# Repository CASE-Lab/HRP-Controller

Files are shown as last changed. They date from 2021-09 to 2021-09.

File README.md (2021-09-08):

# Unicorn HRP Controller

ROS and ROS2 packages for controller unicorn demo with HRP and SP. Also includes microcontroller code for controlling lights, actuators and distance sensors.

## Repository content

* catkin_ws
  * Contains a subset of the code from the [Husqvarna Research Platform](https://github.com/HusqvarnaResearch/hrp) repository.
    Gazebo simulation parts have been removed and only the necessary packages for control of the HRP hardware remain.
  
* colcon_ws
  * hw_controller:
    
    ROS2 node that communicates via serial to the microcontroller that is responsible for interfacing with the garbage tipper, garbage sensors (detects if there is garbage placed on the platform), distance sensors for collision avoidance and LED light strips for status indication.
    
  * unicorn_hrp:
    
    ROS2 node that controls the HRP hardware
    
  * hrp_msgs:
    
    Custom ROS messages
  
* hw-interface

  * Holds code for the microcontroller that interfaces directly with the additional sensors and actuators added to the HRP. Is controlled by the ROS 2 node hw_controller.

## Installation

The current system has been tested on either a Nvidia Jetson Nano or Jetson Xavier NX. The following dependencies need to be installed for the system to work properly:

* ROS2 eloquent [guide](https://index.ros.org/doc/ros2/Installation/Eloquent/Linux-Install-Debians/)

* ROS melodic [guide](http://wiki.ros.org/melodic/Installation/Ubuntu)

* ROS Bridge
  
Used to run a dynamic bridge that translates topics between the ROS2 and ROS. Can be installed by running:
  
  ```bash
  sudo apt-get update
  sudo apt install ros-eloquent-ros1-bridge
```
  
* [Pyserial](https://pypi.org/project/pyserial/) 
  
Needed for serial communication with the microcontroller hardware.
  
* GNU Screen 
  
  Used for the hrp_start.sh script that starts up the system
  Check out this [Quick Reference](https://gist.github.com/jctosta/af918e1618682638aa82) on how to use Screen.

By default Ubuntu does not allow users access to system serial ports. To solve this we need to add the current user to the dialout group:

```bash
sudo usermod -a -G dialout $USER
```

## Startup

Preparing the HRP for startup

1. Make sure the power switch is in the on position
2. Open the lid and enter code 1111
3. Wait for the HRP to initialize and then press start and close the lid when prompted to

Run the startup shell script from the repository root folder

```bash
./hrp_startup.sh
```

This will launch and automatically connect to a screen sessions with the following windows:

0. ros-bash
   
   Regular terminal window with bash and ROS sourced
   
1. am_driver

   Driver used to communicate with the HRP hardware

2. ros1_bridge

   Bridge used to bidirectionally translate topics from ROS2 and ROS

3. teleop

   Teleoperation and status of the HRP hardware

4. ros2_hw_controller

   ROS2 node for interfacing with microcontroller 

5. ros2_hrp_controller

   ROS2 node for interfacing with am_driver

Troubleshooting:

* am_driver is configured to launch with LOOP_OFF (the HRP in regular operation detects a wire signal to prevent it from going outside a specific area) but this does not always take effect. If this is the case navigate to the teleop window in screen and set LOOP_OFF manually

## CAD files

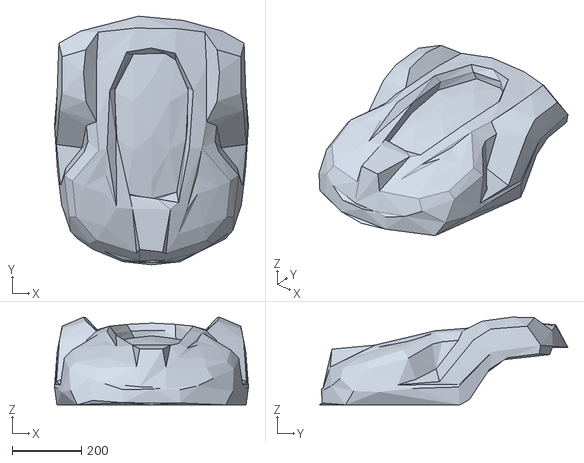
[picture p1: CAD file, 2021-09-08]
catkin_ws/src/am_description/urdf/am_chassis.stl
559.2 x 716.8 x 252.9

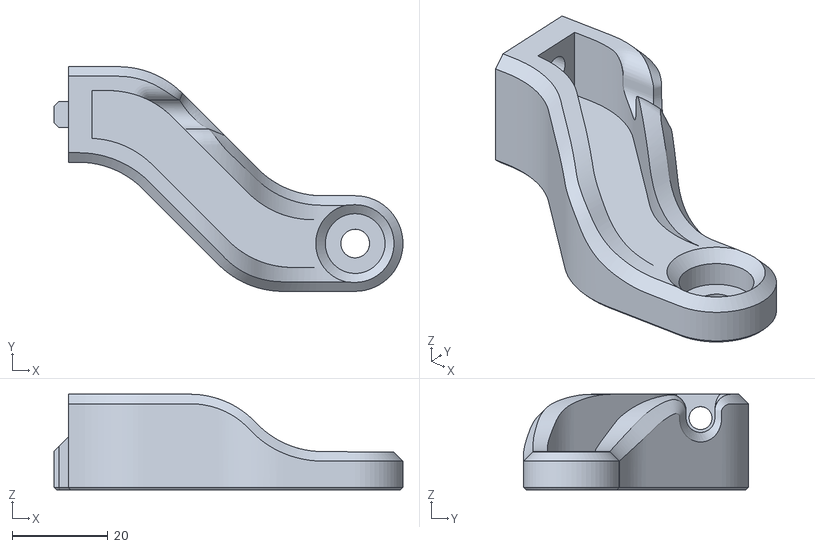
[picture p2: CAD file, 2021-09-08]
hardware/CAD_Garbage_Holder/ManufaturingFiles/RodHolder_Front3.stl
73.0 x 47.0 x 20.0

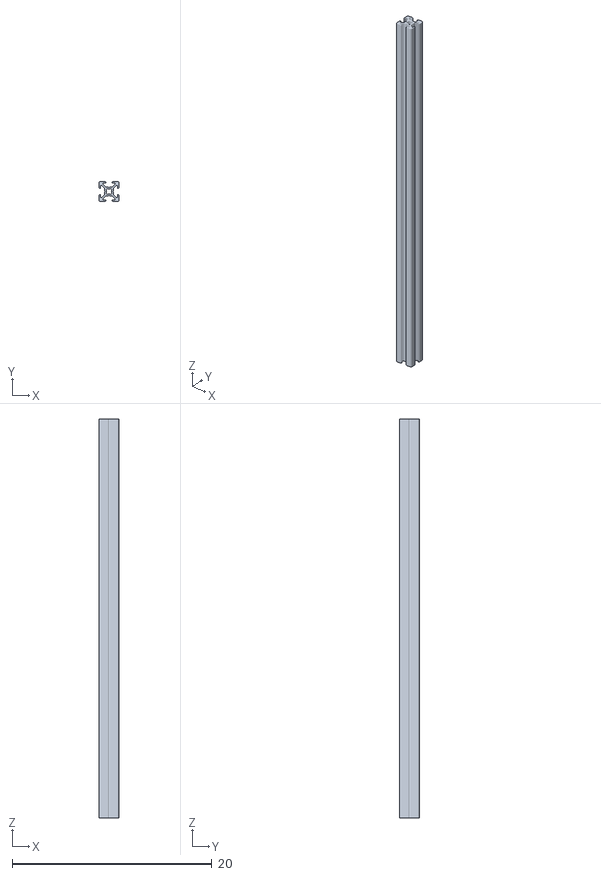
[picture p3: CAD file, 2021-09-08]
hardware/CAD_Garbage_Holder/Parts/Rexroth-3 842 992 888_230MM.stl
2.00 x 2.00 x 40.0

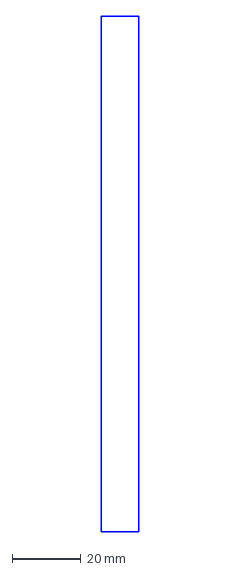
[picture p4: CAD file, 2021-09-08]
hardware/rgb-led-pcb/Outline.dxf
10.8 x 149.6 mm

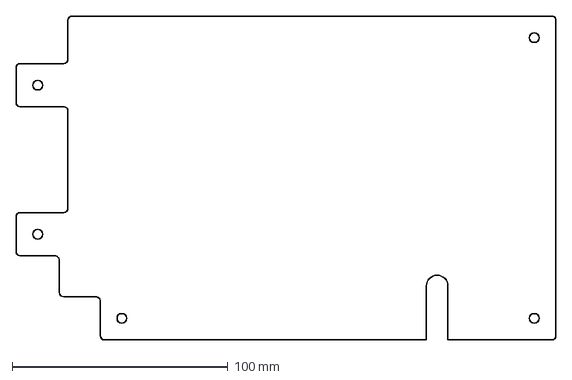
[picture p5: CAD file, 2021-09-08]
hardware/CAD_Garbage_Holder/ManufaturingFiles/SideAcrylicSheet.dxf
250.0 x 150.0 mm

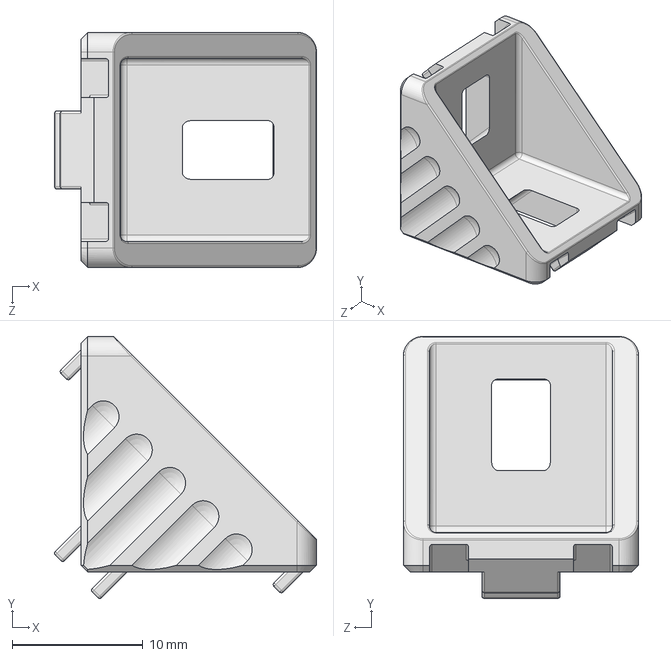
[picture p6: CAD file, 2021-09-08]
hardware/CAD_Garbage_Holder/Parts/Rexroth-3 842 523 508.step
20.0 x 20.0 x 18.0 mm

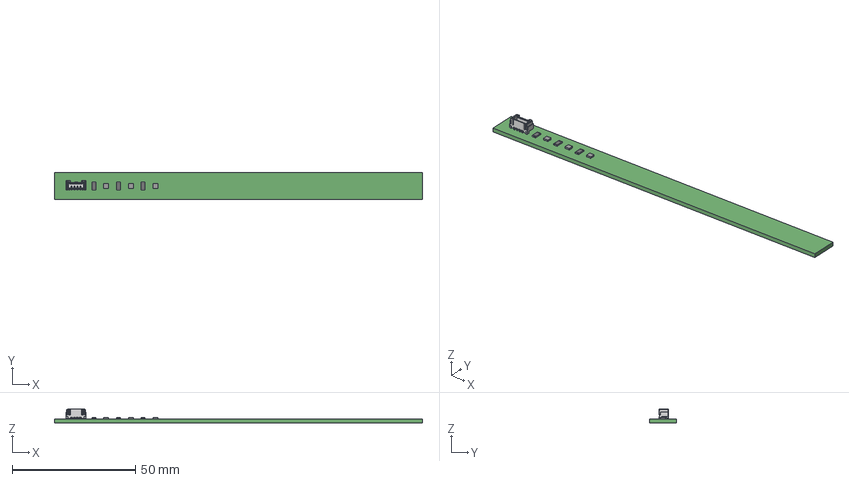
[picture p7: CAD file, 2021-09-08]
hardware/rgb-led-pcb/rgb-led-pcb.step
149.6 x 10.8 x 5.81 mm

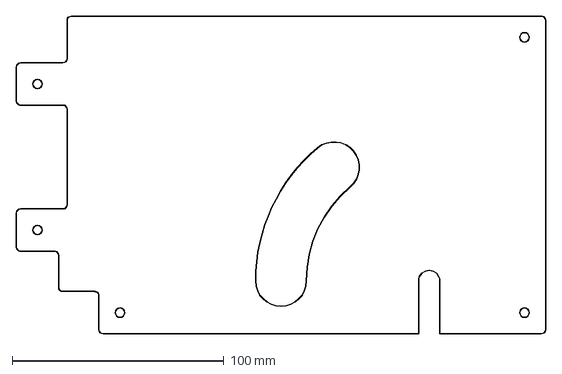
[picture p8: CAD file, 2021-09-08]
hardware/CAD_Garbage_Holder/ManufaturingFiles/SideAcrylicSheet_WithOpening.dxf
250.0 x 150.0 mm

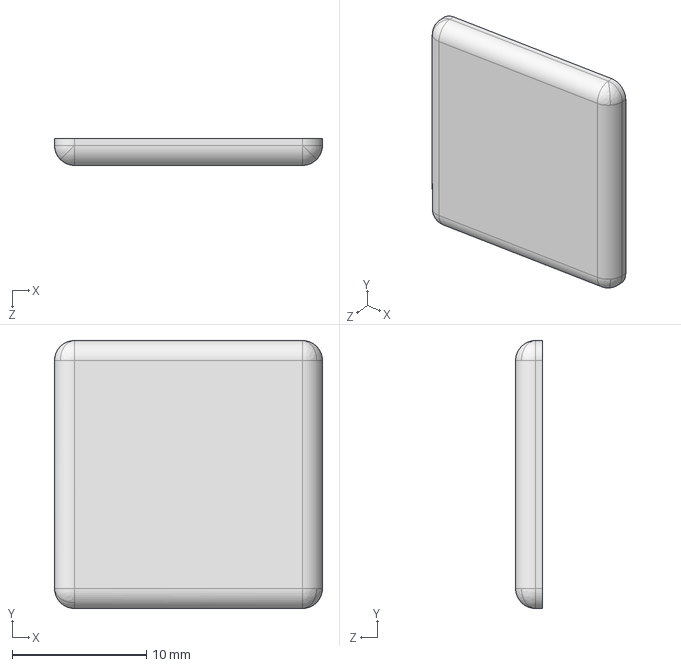
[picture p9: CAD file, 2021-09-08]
hardware/CAD_Garbage_Holder/Parts/Rexroth-3 842 517 243.step
20.0 x 20.0 x 2.00 mm

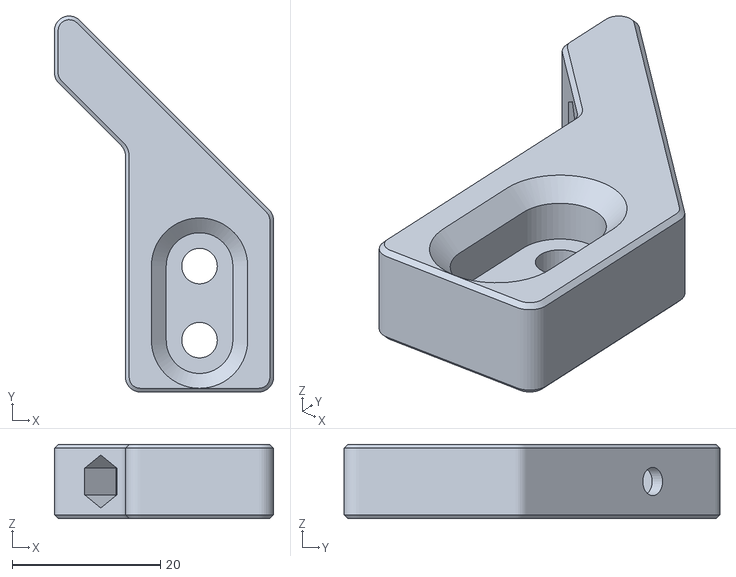
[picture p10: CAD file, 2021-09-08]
hardware/CAD_Garbage_Holder/ManufaturingFiles/UpperAcrylicSheetHolder_MIR.stl
29.6 x 50.8 x 10.0

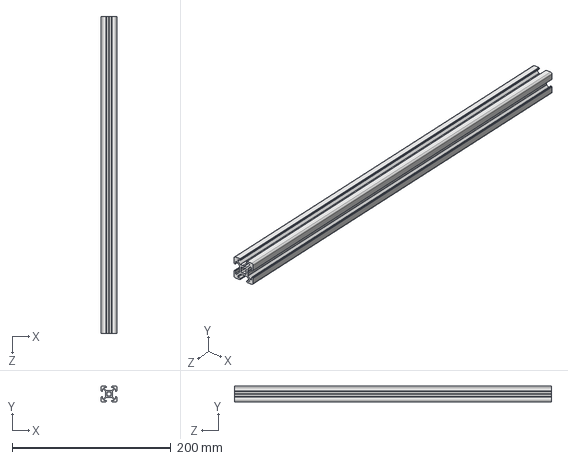
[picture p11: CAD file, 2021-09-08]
hardware/CAD_Garbage_Holder/Parts/Rexroth-3 842 992 888_400MM.step
20.0 x 20.0 x 400.0 mm

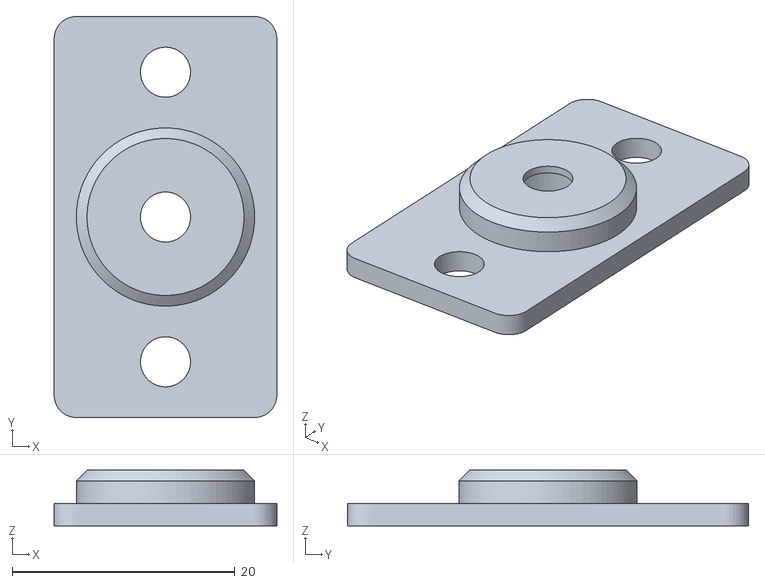
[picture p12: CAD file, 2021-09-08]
hardware/CAD_Garbage_Holder/ManufaturingFiles/LinearActuatorHolder_FlatHead.stl
20.0 x 36.0 x 5.00

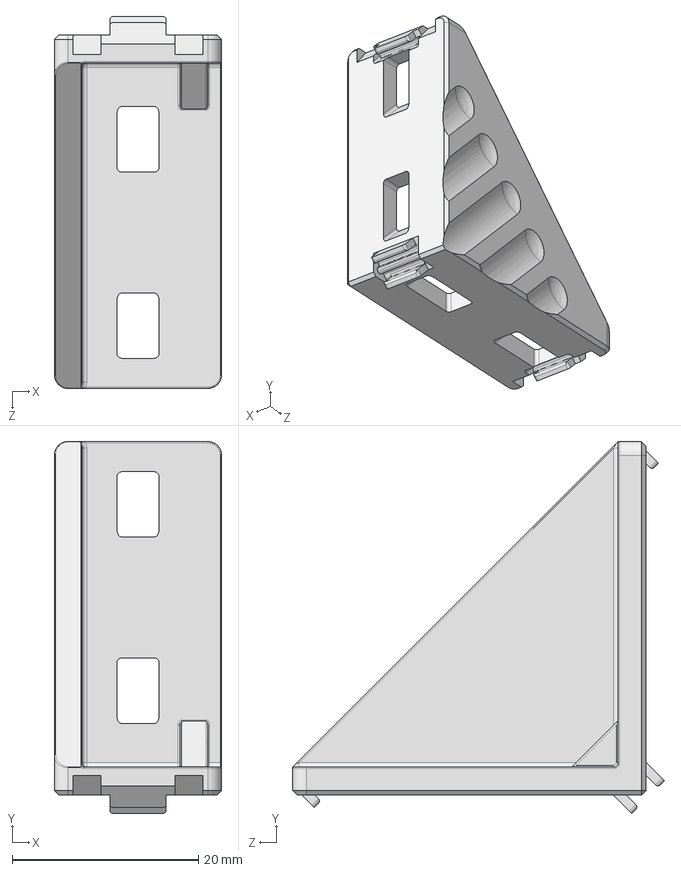
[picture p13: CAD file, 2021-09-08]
hardware/CAD_Garbage_Holder/Parts/Rexroth-3 842 523 517.step
18.0 x 40.0 x 40.0 mm

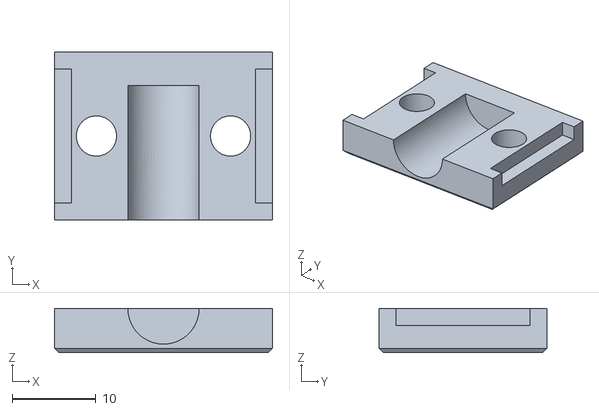
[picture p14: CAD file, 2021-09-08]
hardware/CAD_Garbage_Holder/ManufaturingFiles/SideAcrylicSheetRodHolder_1.stl
26.0 x 20.0 x 5.25

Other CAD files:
hardware/CAD_Garbage_Holder/Parts/LD3 Standard.STEP
hardware/CAD_Garbage_Holder/ManufaturingFiles/BackAcrylicSheet.dxf
hardware/CAD_Garbage_Holder/ManufaturingFiles/BottomAcrylicSheetHolder.stl
hardware/CAD_Garbage_Holder/ManufaturingFiles/SideAcrylicSheetRodHolder_2.stl
hardware/CAD_Garbage_Holder/ManufaturingFiles/BottomAcrylicSheet.dxf
hardware/CAD_Garbage_Holder/ManufaturingFiles/BottomAcrylicSheetRodHolder_1.stl
hardware/CAD_Garbage_Holder/ManufaturingFiles/BottomAcrylicSheetRodHolder_2.stl
hardware/CAD_Garbage_Holder/ManufaturingFiles/Bumper.stl
hardware/CAD_Garbage_Holder/ManufaturingFiles/CableHolder.stl
hardware/CAD_Garbage_Holder/ManufaturingFiles/Controller_PCB_outline.dxf
hardware/CAD_Garbage_Holder/ManufaturingFiles/DistanceSensorHolder.stl
hardware/CAD_Garbage_Holder/ManufaturingFiles/HRP_button_glass.dxf
hardware/CAD_Garbage_Holder/ManufaturingFiles/HolderBack.stl
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

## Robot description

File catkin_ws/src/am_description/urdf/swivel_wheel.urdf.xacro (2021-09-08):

<?xml version="1.0"?>
<robot name="swivel_wheel" xmlns:xacro="http://www.ros.org/wiki/xacro">

  <!-- Wheels -->
<!--
  <xacro:property name="wheel_radius" value="0.125" />
  <xacro:property name="wheel_height" value="0.032" />
-->
  <xacro:property name="wheel_mass" value="0.5" /> <!-- in kg-->

<!--
  <xacro:property name="base_x_origin_to_wheel_origin" value="0.25" />
  <xacro:property name="base_y_origin_to_wheel_origin" value="0.3" />
  <xacro:property name="base_z_origin_to_wheel_origin" value="0.0" />
-->

  <xacro:macro name="cylinder_inertia" params="m r h">
    <inertia ixx="${m*(3*r*r+h*h)/12}" ixy="0" ixz="0" iyy="${m*(3*r*r+h*h)/12}" iyz="0" izz="${m*r*r/2}" />
  </xacro:macro>

  <xacro:macro name="swivel_arm" params="lr index l offset">
    <link name="sw_arm_${lr}_${index}">

      <inertial>
        <mass value="0.01" />
        <origin xyz="0 0 0" />
        <cylinder_inertia m="0.01" r="0.004" h="${l}" />
      </inertial>

      <visual>
        <geometry>
          <cylinder radius="0.004" length="${l}" />
        </geometry>
        <material name="silver">
          <color rgba="0.3 0.3 0.3 1" />
        </material>
        <origin rpy="0 0 0" xyz="${offset}" />
      </visual>
    </link>
  </xacro:macro>

  <xacro:macro name="swivel_wheel" params="fb lr parent translateX translateY translateZ wheel_radius wheel_height flip"> <!--fb : front, back ; lr: left, right -->

    <!-- First link connected to parent-->
    <swivel_arm lr="${lr}" index="1" l="0.06" offset="0 0 -0.03" />

    <joint name="sw_arm_${lr}_connect_1" type="continuous">
      <origin xyz="${translateX} ${translateY} ${translateZ}" rpy="0 0 0" />
      <axis xyz="0 0 1" rpy="0 0 0" />
      <parent link="${parent}" />
      <child link="sw_arm_${lr}_1" />
      <limit effort="100" velocity="100" />
      <joint_properties damping="0.0" friction="0.0" />
    </joint>

    <!-- Second link connected to first-->
    <swivel_arm lr="${lr}" index="2" l="0.04" offset="0 0 0.02" />

    <joint name="sw_arm_${lr}_connect_2" type="fixed">
      <origin rpy="1.5707 0 0" xyz="0 0 -0.06" />
      <parent link="sw_arm_${lr}_1" />
      <child link="sw_arm_${lr}_2" />
    </joint>

    <!-- Third link connected to second-->
    <swivel_arm lr="${lr}" index="3" l="0.06" offset="0 0 -0.03" />

    <joint name="sw_arm_${lr}_connect_3" type="fixed">
      <origin rpy="-1.5707 0 -0.78" xyz="0 0 0.04" />
      <parent link="sw_arm_${lr}_2" />
      <child link="sw_arm_${lr}_3" />
    </joint>

    <!-- Fourth link connected to third-->
    <swivel_arm lr="${lr}" index="4" l="0.04" offset="0 0 -0.02" />

    <joint name="sw_arm_${lr}_connect_4" type="fixed">
      <origin rpy="1.5707 0 0" xyz="0 0 -0.060" />
      <parent link="sw_arm_${lr}_3" />
      <child link="sw_arm_${lr}_4" />
    </joint>

    <!-- Wheel connected to fourth-->
    <link name="${fb}_${lr}_swivel_wheel">
      <visual>
        <origin xyz="0 0 0" rpy="${flip*M_PI/2} 0 0" />
        <geometry>
          <cylinder length="${wheel_height}" radius="${wheel_radius}" />
        </geometry>
        <material name="Black" />
      </visual>
      <collision>
        <origin xyz="0 0 0" rpy="0 0 0" />
        <geometry>
          <cylinder length="${wheel_height}" radius="${wheel_radius}" />
        </geometry>
      </collision>
      <inertial>
        <mass value="${wheel_mass}" />
        <origin xyz="0 0 0" />
        <cylinder_inertia m="${wheel_mass}" r="${wheel_radius}" h="${wheel_height}" />
      </inertial>
    </link>

    <gazebo reference="${fb}_${lr}_swivel_wheel">
      <mu1 value="0.8" />
      <mu2 value="0.8" />
      <kp value="10000000.0" />
      <kd value="1.0" />
      <fdir1 value="1 0 0" />
      <material>Gazebo/Black</material>
      <turnGravityOff>false</turnGravityOff>
    </gazebo>

    <joint name="${fb}_${lr}_swivel_wheel_joint" type="continuous">
      <parent link="sw_arm_${lr}_4" />
      <child link="${fb}_${lr}_swivel_wheel" />
      <origin rpy="0 0 0" xyz="0 0 -0.04" />
      <axis xyz="0 0 1" rpy="0 0 0" />
      <limit effort="100" velocity="100" />
      <joint_properties damping="0.0" friction="0.0" />
    </joint>


    <!-- Transmission is important to link the joints and the controller -->
<!--
    <transmission name="${fb}_${lr}_swivel_wheel_joint_trans">
      <type>transmission_interface/SimpleTransmission</type>
      <joint name="${fb}_${lr}_swivel_wheel_joint">
        <hardwareInterface>EffortJointInterface</hardwareInterface>
      </joint>
      <actuator name="${fb}_${lr}_swivel_wheel_joint_motor">
        <hardwareInterface>EffortJointInterface</hardwareInterface>
        <mechanicalReduction>1</mechanicalReduction>
      </actuator>
    </transmission>
-->


  </xacro:macro>
</robot>

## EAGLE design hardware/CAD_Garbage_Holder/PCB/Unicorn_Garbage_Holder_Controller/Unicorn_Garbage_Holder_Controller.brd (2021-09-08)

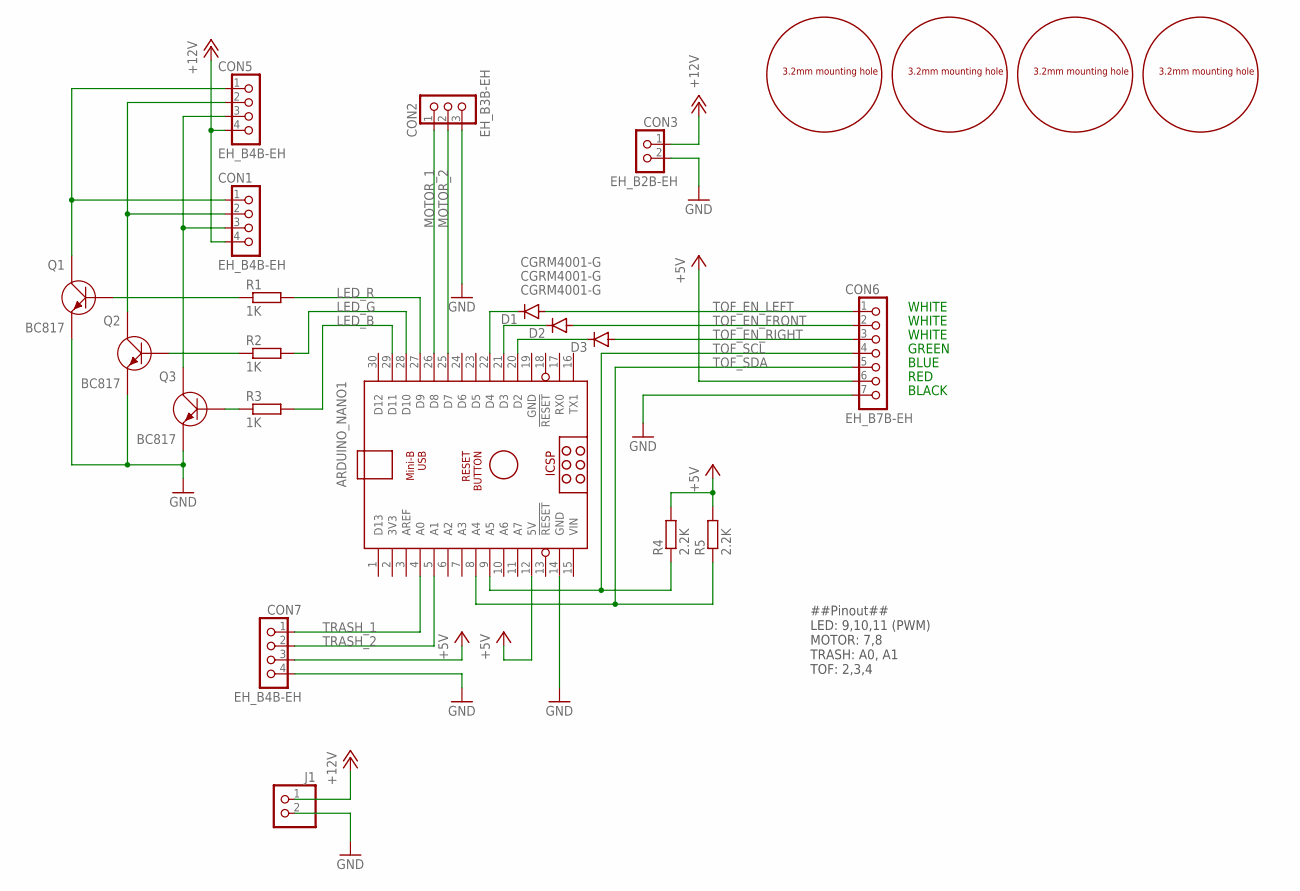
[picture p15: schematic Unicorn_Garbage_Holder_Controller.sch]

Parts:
ARDUINO_NANO1: ARDUINO_NANO
CON1, CON5, CON7: EH_B4B-EH; B4B-EH
CON2: EH_B3B-EH; B3B-EH
CON3: EH_B2B-EH; B2B-EH
CON6: EH_B7B-EH; B7B-EH
D1, D2, D3: CGRM4001-G; SOD-123_MINI-SMA
J1: 1751248
Q1, Q2, Q3: BC817; SOT23
R1, R2, R3: 1K; R0603
R4, R5: 2.2K; R0603
U$5, U$6, U$7, U$8: M3_MOUNTING_HOLE

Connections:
+5V: ARDUINO_NANO1.12 (5V), CON6.6, CON7.3, R4.2, R5.2
+12V: CON1.4, CON3.1, CON5.4, J1.1
GND: ARDUINO_NANO1.14 (GND), ARDUINO_NANO1.19 (GND), CON2.3, CON3.2, CON6.7, CON7.4, J1.2, Q1.2 (E), Q2.2 (E), Q3.2 (E)
LED_B: ARDUINO_NANO1.29 (D11), R3.2
LED_G: ARDUINO_NANO1.28 (D10), R2.2
LED_R: ARDUINO_NANO1.27 (D9), R1.2
MOTOR_1: ARDUINO_NANO1.26 (D8), CON2.1
MOTOR_2: ARDUINO_NANO1.25 (D7), CON2.2
unnamed: Q1.1 (B), R1.1
unnamed: Q2.1 (B), R2.1
unnamed: Q3.1 (B), R3.1
unnamed: CON1.1, CON5.1, Q1.3 (C)
unnamed: CON1.2, CON5.2, Q2.3 (C)
unnamed: CON1.3, CON5.3, Q3.3 (C)
unnamed: ARDUINO_NANO1.22 (D4), D1.C
unnamed: ARDUINO_NANO1.21 (D3), D2.C
unnamed: ARDUINO_NANO1.20 (D2), D3.C
TOF_EN_FRONT: CON6.2, D2.A
TOF_EN_LEFT: CON6.1, D1.A
TOF_EN_RIGHT: CON6.3, D3.A
TOF_SCL: ARDUINO_NANO1.9 (A5), CON6.4, R4.1
TOF_SDA: ARDUINO_NANO1.8 (A4), CON6.5, R5.1
TRASH_1: ARDUINO_NANO1.4 (A0), CON7.1
TRASH_2: ARDUINO_NANO1.5 (A1), CON7.2
VIN: ARDUINO_NANO1.15 (VIN)

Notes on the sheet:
##Pinout## LED: 9,10,11 (PWM) MOTOR: 7,8 TRASH: A0, A1 TOF: 2,3,4
BLUE
GREEN
WHITE
RED
BLACK

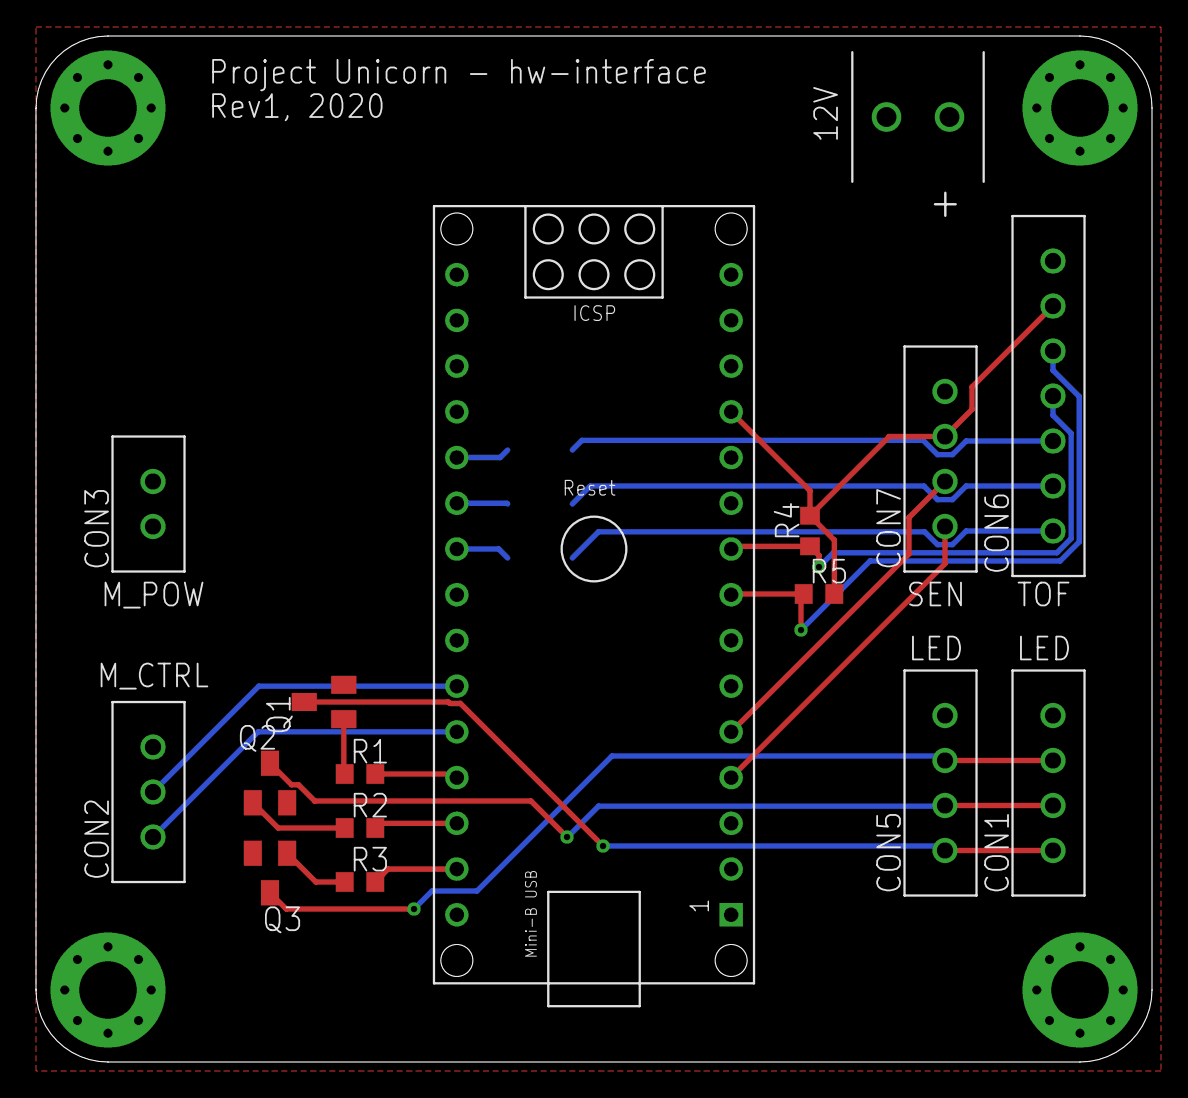
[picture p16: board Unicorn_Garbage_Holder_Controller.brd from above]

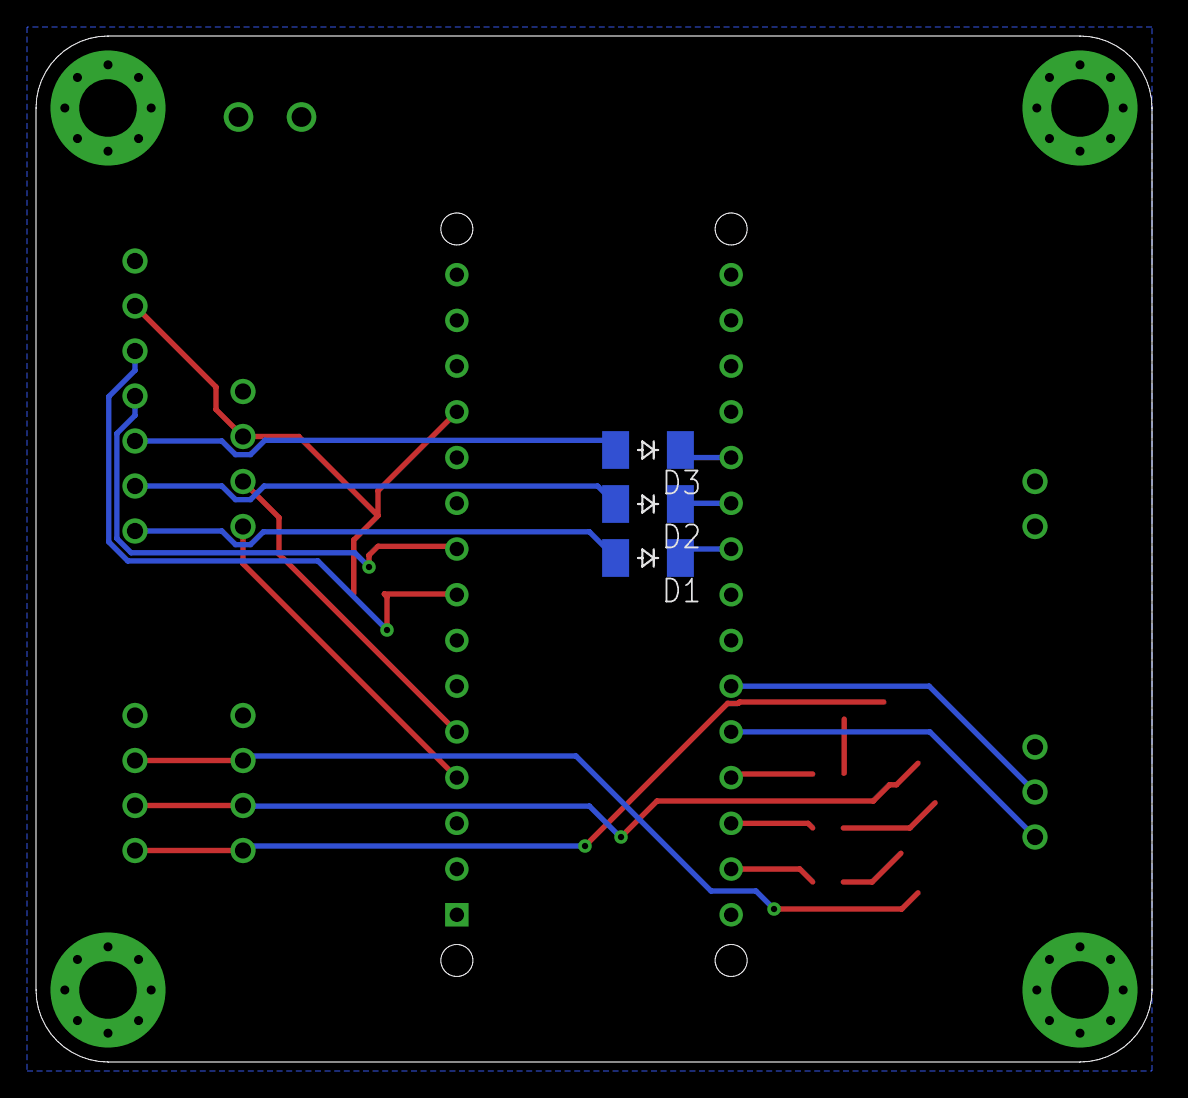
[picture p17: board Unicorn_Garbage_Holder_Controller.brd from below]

Board: 2 copper layers, 62.0 x 57.0 mm, 23 parts (3 on the bottom side), 24 nets.

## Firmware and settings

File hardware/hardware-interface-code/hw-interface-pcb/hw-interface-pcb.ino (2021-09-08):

#include "src/Adafruit-VL530X/Adafruit_VL53L0X.h"
#include "TrashActuator.h"

//all serial commands are sent in a single byte where only the latest
//command is considered

#define NEWLINE "\n"

//defenition of serial commands:
#define ACTUATOR_MASK   0b00000011
#define ACTUATOR_SHIFT  0
#define COLOR_MASK      0b00011100
#define COLOR_SHIFT     2

// address we will assign if dual sensor is present
#define LOXR_ADDRESS 0x30
#define LOXF_ADDRESS 0x31
// last one will be left with default adress 0x29

// set the pins to shutdown
#define SHT_LOXR 2 //right (diode connected
#define SHT_LOXF 3 //front (diode connected)
#define SHT_LOXL 4 //left  (diode connected)

//define sensor states
#define LOX_OUT_OF_RANGE 4
#define LOX_ERROR -2

// objects for the vl53l0x
Adafruit_VL53L0X loxRight = Adafruit_VL53L0X();
Adafruit_VL53L0X loxFront = Adafruit_VL53L0X();
Adafruit_VL53L0X loxLeft = Adafruit_VL53L0X();

//define pins for indicator light
#define R_OUT (uint8_t)9
#define G_OUT (uint8_t)10
#define B_OUT (uint8_t)11

//define colors for indicator light
#define INDICATOR_OFF 0
#define INDICATOR_RED 1
#define INDICATOR_BLUE 2
#define INDICATOR_GREEN 3
#define INDICATOR_YELLOW 4
#define INDICATOR_WHITE 5

//global variable for current color
uint8_t currentColor;

//function prototypes for indicator light
void setColor(uint8_t color);
void initIndicator();

// set the pins for motor control
#define IN1 8
#define IN2 7

// sets actuation time in ms
#define ACTUATION_TIME 4000

// object for trash tipper
TrashActuator actuator = TrashActuator(IN1, IN2, ACTUATION_TIME);

//function prototypes:
void setID();
int readRange(Adafruit_VL53L0X *sensor);

//pin defenitions for trash sensors
#define PROX_PIN1 A0
#define PROX_PIN2 A1

//trash status values
#define TRASH_FULL 1
#define TRASH_EMPTY 0
#define TRASH_FULL_PATTERN   0b00000011 //sets how many consequtive readings need to be the same for state switch
#define TRASH_EMPTY_PATTERN  0b00000000
#define TRASH_PATTERN_MASK   0b00000011 //sets how many consequtive readings need to be the same for state switch

void setup() {
  Serial.begin(115200);
  // wait until serial port opens for native USB devices:
  while (! Serial) { delay(1); }

  //configure adress for all 3 sensors:
  setID();

  //set actuator to down position
  actuator.setActuatorCommand(ACTUATOR_CMD_DOWN
  , millis());
  //delay(ACTUATION_TIME);

  //configure trash sensors pins as input:
  pinMode(PROX_PIN1, INPUT);
  pinMode(PROX_PIN2, INPUT);

  initIndicator();
  
  //testing colors:
  setColor(INDICATOR_RED);
  delay(100);
  setColor(INDICATOR_GREEN);
  delay(100);
  setColor(INDICATOR_BLUE);
  delay(100);
  setColor(INDICATOR_YELLOW);
  delay(100);
  setColor(INDICATOR_WHITE);
  delay(100);
  setColor(INDICATOR_GREEN);   //default standby color
}

void loop() {

  //set up static local variables;
  static int rightRange, leftRange, frontRange;
  static unsigned long timeInterval;
  static char tempCmd;
  static uint8_t cmd = 0;
  static uint8_t trashStatus;
  static uint8_t trashStatusDebounce = 0;
  static uint8_t cmdColor;
  static uint8_t cmdActuator;
  uint8_t prevCmd = cmd;

  // grab latest command (reads serial buffer until empty)
  while( (tempCmd = Serial.read()) != -1 ) {
    cmd = tempCmd;
  }

  //check if command has changed:
  if(cmd!=prevCmd) {
    // Serial.print(F("NEW CMD: "));
    // Serial.println(cmd, BIN);
    //parse commands:
    cmdActuator = (cmd & ACTUATOR_MASK) >> ACTUATOR_SHIFT;
    cmdColor = (cmd & COLOR_MASK) >> COLOR_SHIFT;
    // Serial.print(F("NEW CMD ACTUATOR: "));
    // Serial.println(cmdActuator, BIN);
    // Serial.print(F("NEW CMD COLOR: "));
    // Serial.println(cmdColor, BIN);

    //set commands:
    actuator.setActuatorCommand(cmdActuator, millis());
    setColor(cmdColor);
  }

  //read distances:
  rightRange = readRange(&loxRight);
  leftRange = readRange(&loxLeft);
  frontRange = readRange(&loxFront);

  //check sensor error status:
  while(rightRange == LOX_ERROR || leftRange == LOX_ERROR || frontRange == LOX_ERROR) {
    //reset sensors:
    setID();
    //read distances:
    rightRange = readRange(&loxRight);
    leftRange = readRange(&loxLeft);
    frontRange = readRange(&loxFront);
  }

  //read status of trash proximity sensors
  //if any of the sensor are active low then trash is considered detected

  if (!digitalRead(PROX_PIN1) || !digitalRead(PROX_PIN2)) {
    trashStatusDebounce = trashStatusDebounce << 1;
    trashStatusDebounce |= 1;
  }
  else {
    trashStatusDebounce = trashStatusDebounce << 1;
  }

  if ( (trashStatusDebounce & TRASH_PATTERN_MASK) == TRASH_FULL_PATTERN) {
    trashStatus = TRASH_FULL;
  }
  else if ( (trashStatusDebounce & TRASH_PATTERN_MASK) == TRASH_EMPTY_PATTERN) {
    trashStatus = TRASH_EMPTY;
  }

  //trash debounce debug:
/*   Serial.print("Trash Status: ");
  Serial.println(trashStatus);
  Serial.print("History: ");
  Serial.println(trashStatusDebounce, BIN); */
  
  //indicate start of packet
  Serial.print(F("PACKET:"));
  Serial.print(NEWLINE);
  //print range over serial:
  Serial.print(F("R: "));
  Serial.print(rightRange);
  Serial.print(NEWLINE);
  Serial.print(F("L: "));
  Serial.print(leftRange);
  Serial.print(NEWLINE);
  Serial.print(F("F: "));
  Serial.print(frontRange);
  Serial.print(NEWLINE);

  //print state of trash actuator
  Serial.print(F("A: "));
  Serial.print(actuator.getActuatorState(millis()));
  Serial.print(NEWLINE);

  //print state of trash carrying
  Serial.print(F("T: "));
  Serial.print(trashStatus);
  Serial.print(NEWLINE);

  //print state of ligt indicator
  Serial.print(F("I: "));
  Serial.print(currentColor);
  Serial.print(NEWLINE);
}


void setID() {
  Serial.println(F("Resetting sensors"));
  // shutdown all sensors:
  pinMode(SHT_LOXR, OUTPUT);
  pinMode(SHT_LOXF, OUTPUT);
  pinMode(SHT_LOXL, OUTPUT);

  digitalWrite(SHT_LOXR, LOW);
  digitalWrite(SHT_LOXF, LOW);
  digitalWrite(SHT_LOXL, LOW);

  delay(10);

  // enable right sensor:
  pinMode(SHT_LOXR, INPUT);
  delay(10);

  // initing right
  if(!loxRight.begin(LOXR_ADDRESS)) {
    Serial.println(F("Right failed"));
    while(1);
  }
  delay(10);

  //enable front sensor:
  pinMode(SHT_LOXF, INPUT);
  delay(10);

  //initing front
  if(!loxFront.begin(LOXF_ADDRESS)) {
    Serial.println(F("Front failed"));
    while(1);
  }
  delay(10);

  //enable left sensor
  pinMode(SHT_LOXL, INPUT);
  delay(10);
  
  //initing left (default adress)
  if(!loxLeft.begin()) {
    Serial.println(F("Left failed"));
    while(1);
  }
  delay(10);
}

int readRange(Adafruit_VL53L0X *sensor) {
  int status;
  // returns -1 if sensor is out of range
  // returns range  in mm if sensor is in range
  // this holds the measurement (what is this struct -  how much memmory?)
  static VL53L0X_RangingMeasurementData_t measurement;
  // get measurement with debug disabled
  status = sensor->getSingleRangingMeasurement(&measurement, false);
  //Serial.print(F("Status: "));
  //Serial.println(status);
  if(status == VL53L0X_ERROR_NONE) {
    if(measurement.RangeStatus != LOX_OUT_OF_RANGE) {
      return measurement.RangeMilliMeter;
    }
    else {
      return -1;
    }
  }
  else {
    //did not manage to read distance correctly
    return LOX_ERROR;
  }

}

void initIndicator() {
  pinMode(R_OUT, OUTPUT);
  pinMode(G_OUT, OUTPUT);
  pinMode(B_OUT, OUTPUT);

  digitalWrite(R_OUT, LOW);
  digitalWrite(G_OUT, LOW);
  digitalWrite(B_OUT, LOW);

  currentColor = INDICATOR_OFF;
}

void setColor(uint8_t color) {
    //Serial.println(F("Setting color"));
    currentColor = color;
    switch (color) {
    case INDICATOR_OFF:
      digitalWrite(R_OUT, LOW);
      digitalWrite(G_OUT, LOW);
      digitalWrite(B_OUT, LOW);
      break;

    case INDICATOR_RED:
      digitalWrite(R_OUT, HIGH);
      digitalWrite(G_OUT, LOW);
      digitalWrite(B_OUT, LOW);
      break;

    case INDICATOR_BLUE:
      digitalWrite(R_OUT, LOW);
      digitalWrite(G_OUT, LOW);
      digitalWrite(B_OUT, HIGH);
      break;

    case INDICATOR_GREEN:
      digitalWrite(R_OUT, LOW);
      digitalWrite(G_OUT, HIGH);
      digitalWrite(B_OUT, LOW);
      break;

    case INDICATOR_YELLOW:
      digitalWrite(R_OUT, HIGH);
      digitalWrite(G_OUT, HIGH);
      digitalWrite(B_OUT, LOW);
      break;

    case INDICATOR_WHITE:
      digitalWrite(R_OUT, HIGH);
      digitalWrite(G_OUT, HIGH);
      digitalWrite(B_OUT, HIGH);
      break;

    default:
        digitalWrite(R_OUT, LOW);
        digitalWrite(G_OUT, LOW);
        digitalWrite(B_OUT, LOW);
        break;
    }
}

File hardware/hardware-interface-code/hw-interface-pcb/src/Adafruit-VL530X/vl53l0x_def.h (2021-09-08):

/*******************************************************************************
Copyright 2016, STMicroelectronics International N.V.
All rights reserved.

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
THIS SOFTWARE IS PROVIDED BY THE COPYRIGHT HOLDERS AND CONTRIBUTORS "AS IS" AND
ANY EXPRESS OR IMPLIED WARRANTIES, INCLUDING, BUT NOT LIMITED TO, THE IMPLIED
WARRANTIES OF MERCHANTABILITY, FITNESS FOR A PARTICULAR PURPOSE, AND
NON-INFRINGEMENT OF INTELLECTUAL PROPERTY RIGHTS ARE DISCLAIMED.
IN NO EVENT SHALL STMICROELECTRONICS INTERNATIONAL N.V. BE LIABLE FOR ANY
DIRECT, INDIRECT, INCIDENTAL, SPECIAL, EXEMPLARY, OR CONSEQUENTIAL DAMAGES
(INCLUDING, BUT NOT LIMITED TO, PROCUREMENT OF SUBSTITUTE GOODS OR SERVICES;
LOSS OF USE, DATA, OR PROFITS; OR BUSINESS INTERRUPTION) HOWEVER CAUSED AND
ON ANY THEORY OF LIABILITY, WHETHER IN CONTRACT, STRICT LIABILITY, OR TORT
(INCLUDING NEGLIGENCE OR OTHERWISE) ARISING IN ANY WAY OUT OF THE USE OF THIS
SOFTWARE, EVEN IF ADVISED OF THE POSSIBILITY OF SUCH DAMAGE.
*******************************************************************************/

/**
 * @file VL53L0X_def.h
 *
 * @brief Type definitions for VL53L0X API.
 *
 */

#ifndef _VL53L0X_DEF_H_
#define _VL53L0X_DEF_H_

#ifdef __cplusplus
extern "C" {
#endif

/** @defgroup VL53L0X_globaldefine_group VL53L0X Defines
 *	@brief	  VL53L0X Defines
 *	@{
 */

/** PAL SPECIFICATION major version */
#define VL53L0X10_SPECIFICATION_VER_MAJOR 1
/** PAL SPECIFICATION minor version */
#define VL53L0X10_SPECIFICATION_VER_MINOR 2
/** PAL SPECIFICATION sub version */
#define VL53L0X10_SPECIFICATION_VER_SUB 7
/** PAL SPECIFICATION sub version */
#define VL53L0X10_SPECIFICATION_VER_REVISION 1440

/** VL53L0X PAL IMPLEMENTATION major version */
#define VL53L0X10_IMPLEMENTATION_VER_MAJOR 1
/** VL53L0X PAL IMPLEMENTATION minor version */
#define VL53L0X10_IMPLEMENTATION_VER_MINOR 0
/** VL53L0X PAL IMPLEMENTATION sub version */
#define VL53L0X10_IMPLEMENTATION_VER_SUB 9
/** VL53L0X PAL IMPLEMENTATION sub version */
#define VL53L0X10_IMPLEMENTATION_VER_REVISION 3673

/** PAL SPECIFICATION major version */
#define VL53L0X_SPECIFICATION_VER_MAJOR 1
/** PAL SPECIFICATION minor version */
#define VL53L0X_SPECIFICATION_VER_MINOR 2
/** PAL SPECIFICATION sub version */
#define VL53L0X_SPECIFICATION_VER_SUB 7
/** PAL SPECIFICATION sub version */
#define VL53L0X_SPECIFICATION_VER_REVISION 1440

/** VL53L0X PAL IMPLEMENTATION major version */
#define VL53L0X_IMPLEMENTATION_VER_MAJOR 1
/** VL53L0X PAL IMPLEMENTATION minor version */
#define VL53L0X_IMPLEMENTATION_VER_MINOR 0
/** VL53L0X PAL IMPLEMENTATION sub version */
#define VL53L0X_IMPLEMENTATION_VER_SUB 1
/** VL53L0X PAL IMPLEMENTATION sub version */
#define VL53L0X_IMPLEMENTATION_VER_REVISION 4606
#define VL53L0X_DEFAULT_MAX_LOOP 200
#define VL53L0X_MAX_STRING_LENGTH 8

#include "vl53l0x_device.h"
#include "vl53l0x_types.h"

/****************************************
 * PRIVATE define do not edit
 ****************************************/

/** @brief Defines the parameters of the Get Version Functions
 */
typedef struct {
  uint32_t revision; /*!< revision number */
  uint8_t major;     /*!< major number */
  uint8_t minor;     /*!< minor number */
  uint8_t build;     /*!< build number */
} VL53L0X_Version_t;

/** @brief Defines the parameters of the Get Device Info Functions
 */
typedef struct {
  char Name[VL53L0X_MAX_STRING_LENGTH];
  /*!< Name of the Device e.g. Left_Distance */
  char Type[VL53L0X_MAX_STRING_LENGTH];
  /*!< Type of the Device e.g VL53L0X */
  char ProductId[VL53L0X_MAX_STRING_LENGTH];
  /*!< Product Identifier String	*/
  uint8_t ProductType;
  /*!< Product Type, VL53L0X = 1, VL53L1 = 2 */
  uint8_t ProductRevisionMajor;
  /*!< Product revision major */
  uint8_t ProductRevisionMinor;
  /*!< Product revision minor */
} VL53L0X_DeviceInfo_t;

/** @defgroup VL53L0X_define_Error_group Error and Warning code returned by API
 *	The following DEFINE are used to identify the PAL ERROR
 *	@{
 */

typedef int8_t VL53L0X_Error;

#define VL53L0X_ERROR_NONE ((VL53L0X_Error)0)
#define VL53L0X_ERROR_CALIBRATION_WARNING ((VL53L0X_Error)-1)
/*!< Warning invalid calibration data may be in used
        \a	VL53L0X_InitData()
        \a VL53L0X_GetOffsetCalibrationData
        \a VL53L0X_SetOffsetCalibrationData */
#define VL53L0X_ERROR_MIN_CLIPPED ((VL53L0X_Error)-2)
/*!< Warning parameter passed was clipped to min before to be applied */
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

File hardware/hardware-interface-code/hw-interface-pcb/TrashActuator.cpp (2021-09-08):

#include "TrashActuator.h"
#include "Arduino.h"

TrashActuator::TrashActuator(uint8_t IN1, uint8_t IN2, unsigned long actuationTime) {
    this->IN1 = IN1;
    this->IN2 = IN2;
    this->actuationTime = actuationTime;

    //set up pin outputs
    pinMode(IN1, OUTPUT);
    pinMode(IN2, OUTPUT);

    //set up initial command and output to COAST
    digitalWrite(IN1, LOW);
    digitalWrite(IN2, LOW);

    currentCommand = ACTUATOR_CMD_COAST;

    //initial position when starting is unknown
    actuatorState = ACTUATOR_UNKOWN;

}

void TrashActuator::setActuatorCommand(uint8_t command, unsigned long currentTime) {
    //Serial.println(F("Setting command"));
    if(command == currentCommand) {
        return; //ignore repeated same command
    }
    else {
        currentCommand = command;
    }

    switch (command)
    {
    case ACTUATOR_CMD_UP:
        prevTime = currentTime; //sets timer
        actuatorState = ACTUATOR_UNKOWN;
        //set motor outputs:
        digitalWrite(IN1, HIGH);
        digitalWrite(IN2, LOW);
        break;

    case ACTUATOR_CMD_DOWN:
        //Serial.println(F("CMD: DOWM"));
        prevTime = currentTime; //sets timer
        actuatorState = ACTUATOR_UNKOWN;
        //set motor outputs:
        digitalWrite(IN1, LOW);
        digitalWrite(IN2, HIGH);
        break;

    case ACTUATOR_CMD_COAST:
        actuatorState = ACTUATOR_UNKOWN;
        //set motor outputs:
        digitalWrite(IN1, LOW);
        digitalWrite(IN2, LOW);
        break;

    default:
        //invalid command
        Serial.println(F("ERROR: INVALID COMMAND"));
        break;
    }
}

uint8_t TrashActuator::getActuatorState(unsigned long currentTime) {
    //check if time delta is longer than actuationTime
    if (currentTime - prevTime > actuationTime) {
        switch (currentCommand)
        {
        case ACTUATOR_CMD_DOWN:
            actuatorState = ACTUATOR_DOWN;
            currentCommand = ACTUATOR_CMD_COAST;
            //set motor outputs:
            digitalWrite(IN1, LOW);
            digitalWrite(IN2, LOW);
            break;
        case ACTUATOR_CMD_UP:
            actuatorState = ACTUATOR_UP;
            currentCommand = ACTUATOR_CMD_COAST;
            //set motor outputs:
            digitalWrite(IN1, LOW);
            digitalWrite(IN2, LOW);
            break;
        default:
            break;
        }
    }

    return actuatorState;
}

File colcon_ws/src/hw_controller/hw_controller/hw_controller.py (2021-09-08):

#ROS 2 related imports:
import rclpy
from rclpy.node import Node

#Message imports:
from hrp_msgs.msg import HrpMeasurementSensor
from std_msgs.msg import String

#Other imports:
import time
import serial

class hwController(Node):

    def __init__(self):
        super().__init__('hw_controller')

        #namespace paths
        self.hrp1 = '/hrp/hrp1/'
        self.ga1 = '/ga/ga1/'
        self.ga_s1 = '/ga_s/ga_s1/'
        self.light1 = 'light/light1/'

        #command and state decoding mapping dictionaries

        self.colorCmdDict = {
            "off"   :   0 << 2,
            "red"   :   1 << 2,
            "blue"  :   2 << 2,
            "green" :   3 << 2,
            "yellow":   4 << 2,
            "white" :   5 << 2,
        }

        # decode does not need bit shifting and off is discarded
        self.colorDecodeDict = {
            1 : "red",
            2 : "blue",
            3 : "green",
            4 : "yellow",
            5 : "white",
        }

        self.actuatorCmdDict = {
            "coast" :   0,
            "up"    :   1,
            "down"  :   2,  
        }

        # coast is not SP state and is discarded
        self.actuatorDecodeDict = {
            1 : "up",
            2 : "down",
        }

        self.trashSensorDecodeDict = {
            1 : "on",
            0 : "off",
        }

        self.parsedStateDict = dict.fromkeys(['R', 'L', 'F', 'A' ,'T' ,'I'])

        #variable defenitions
        self.currentColorCmd = self.colorCmdDict["blue"]    # holds current command byte for color
        self.currentActuatorCmd = 0                         # holds current actuator command

        #init of serial com:
        self.ser = self.initSerial()

        #check if serial port is open
        if(self.ser.isOpen()):
            self.get_logger().info("Serial port opened")


        #defining publishers

        self.distSensorPub = self.create_publisher(
        HrpMeasurementSensor,
        self.hrp1+'unicorn_measurement_sensor',
        10)

        self.trashSensorPub = self.create_publisher(
        String,
        self.ga_s1+'controller_state',
        10)

        self.trashActuatorStatePub = self.create_publisher(
        String,
        self.ga1+'controller_state',
        10)

        self.indicatorLightStatePub = self.create_publisher(
        String,
        self.light1+'controller_state',
        10)

        #defining subscribers:

        self.trashActuatorGoalSub = self.create_subscription(
        String,
        self.ga1+'controller_goal',
        self.trashActuatorGoalSubCallback,
        10)

        self.indicatorLightGoalSub = self.create_subscription(
        String,
        self.light1+'controller_goal',
        self.indicatorLightGoalSubCallback,
        10)


        #define timer for serial read
        timer_period = 0.1
        self.timerSerial = self.create_timer(timer_period, self.serialTimerCallback)

    #defining timer callbacks
    
    def serialTimerCallback(self):
        # Check if data is available to read (https://stackoverflow.com/questions/38645060/what-is-the-equivalent-of-serial-available-in-pyserial)
        if self.ser.in_waiting > 0:
            #find start of packet:
            while(self.ser.readline().decode("utf-8") !=  "PACKET:\n"):
                pass
            for _x in range(0, len(self.parsedStateDict)):
                try:
                    line = self.ser.readline().decode("utf-8")
                    [stateType, state] = line.split(": ")
                except ValueError:
                    self.get_logger().warn("Decode or splitting of string failed")
                    return #skips this decode iteration - TODO look into better way to hande this

                if stateType in self.parsedStateDict.keys():
                    try:
                        self.parsedStateDict[stateType] = int(state.strip())
                    except ValueError:
                        self.get_logger().warn("String to int conversion failed!")
                else:
                    self.get_logger().error("INCORRECT SERIAL PARSE KEY")
            print(self.parsedStateDict)

            # publish values to ros topics:
            self.distSensorSend()
            self.trashSensorSend()
            self.trashActuatorStateSend()
            self.indicatorLightStateSend()


    #defining subscriber callbacks

    def indicatorLightGoalSubCallback(self, msg):
        if msg.data in self.colorCmdDict.keys():
            self.currentColorCmd = self.colorCmdDict[msg.data]
            self.sendSerialCommand()
        else:
            self.get_logger().error("Invalid color command: " + msg.data)

    def trashActuatorGoalSubCallback(self, msg):
        if msg.data in self.actuatorCmdDict.keys():
            self.currentActuatorCmd = self.actuatorCmdDict[msg.data]
            self.sendSerialCommand()
        else:
            self.get_logger().error("Invalid actuator command: " + msg.data)

    # defining publishing functions:

    def distSensorSend(self):
        msg = HrpMeasurementSensor()
        msg.f = self.parsedStateDict["F"]
        msg.l = self.parsedStateDict["L"]
        msg.r = self.parsedStateDict["R"]
        self.distSensorPub.publish(msg)

    def trashSensorSend(self):
        msg = String()
        msg.data = self.trashSensorDecodeDict[self.parsedStateDict["T"]]
        self.trashSensorPub.publish(msg)

    def trashActuatorStateSend(self):
        msg = String()
        # check key so we ignore off state (not a SP state)
        if self.parsedStateDict["A"] in self.actuatorDecodeDict.keys():
            msg.data = self.actuatorDecodeDict[self.parsedStateDict["A"]]
            self.trashActuatorStatePub.publish(msg)

    def indicatorLightStateSend(self):
        msg = String()
        # check key so we ignore off state (not a SP state)
        if self.parsedStateDict["I"] in self.colorDecodeDict.keys():
            msg.data = self.colorDecodeDict[self.parsedStateDict["I"]]
            self.indicatorLightStatePub.publish(msg)

    # defining helper functions

    def sendSerialCommand(self):
        # compose command via bitwise and:
        cmd = self.currentColorCmd | self.currentActuatorCmd
        self.get_logger().debug("Serial command: " + "{0:b}".format(cmd) ) 
        packet = bytearray()
        packet.append(cmd)
        self.ser.write(packet)

    def initSerial(self):
        #TODO: update to make these configurable arguments
        #TODO: add exception handling when the port fails to be configured
        # Serial port is instantly opened upon creation (https://pyserial.readthedocs.io/en/latest/pyserial_api.html)
        ser = serial.Serial(
        port='/dev/ttyACM1',
        baudrate=115200,
        timeout = 3)
        return ser

    def closeSerial(self):
        self.ser.close()
        self.get_logger.info("Closing serial port")
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
